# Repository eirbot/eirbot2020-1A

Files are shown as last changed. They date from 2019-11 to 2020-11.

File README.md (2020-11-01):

# EIRBOT 2020-1A : Equipe EIRBOAT 

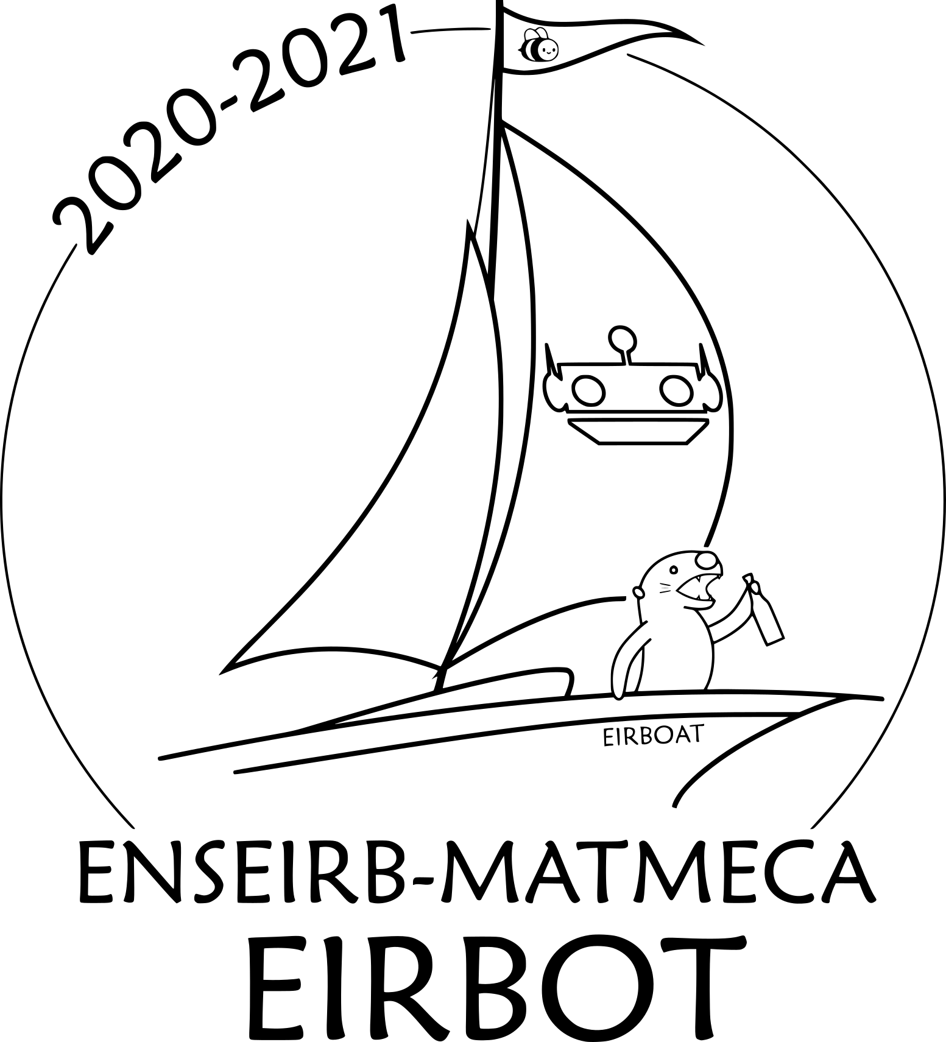
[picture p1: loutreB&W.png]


---

Résultat de l'équipe à l'édition d'octobre 2020 : 24 ième / 51
---

Ceci est le dépôt de l'équipe de 1A de l'association de robotique Eirbot. La
description de l'avancement des différents projets est disponible via la 
[descrition](https://github.com/eirbot/eirbot2020-1A/blob/master/description/descrption.pdf) de nos projets. Le projet se divise en plusieures catégories allant du plus bas au plus au niveau (en terme de raprochement avec le côté physique). 

## Membres
Ce projet est réalisé par les différents membres de Eirbot en première année : 
- Alberty Maxime (SEE)
- Barrais Marius
- Camberlin Erwann (Matmeca)
- Delpeuch Sébastien (Informatique)
- Mangin Lucas
- Moroy Liam
- Neveu Emile
- Pouget Filipe
- Poupon Julien
- Savary Clément (SEE)
- Vaquori Yohann
- Vidal Martin

## Installation 
Le projet est construit avec Cmake, il suffit donc de cloner le projet puis 

```
cd eirbot2020-1A/code/
cd build/
cmake .. 
```

## Éxecution 

Depuis le dossier `build/`

Pour compiler le projet il suffit de faire `make project` en ayant un compilateur
de C++.

Plusieurs méthodes permettent d'exécuter le projet.

En local un `./project` suffit, si la nucléo est branchée via le port USB une
simulation de communication est enclenchée (la nucléo renvoie toujours vrai à
chaque demande). Cela peut demander de faire la commande en super utilisateur ou
changer le chemin d'accès au port USB (ligne 110 de ce
[code](https://github.com/eirbot2020-1A/tree/master/code/rasp/src/main.cc)). 

Pour mettre le projet sur la rasp et donc le robot il faut être connecté au même
wifi que la raspeberry puis faire un `make final`.

En plus de l'exécution des tests sont effectués sur les codes, ils peuvent être
compilés en faisant `make test` puis `./test`. A partir de ce moment des tests
sur tous les modules implémentés sont exécutés, le coverage actuel est de 87%

Finalement un `make doc` permet d'afficher la documentation de nos codes.
Elle est de plus disponible sur notre [page web](https://eirbot.github.io/eirbot2020-1A/md__r_e_a_d_m_e.html)

## Description du projet 
### Mécanique
La mécanique du projet se base sur une architecture octogonale structuré par des
profilés avec la notion d'étage. 

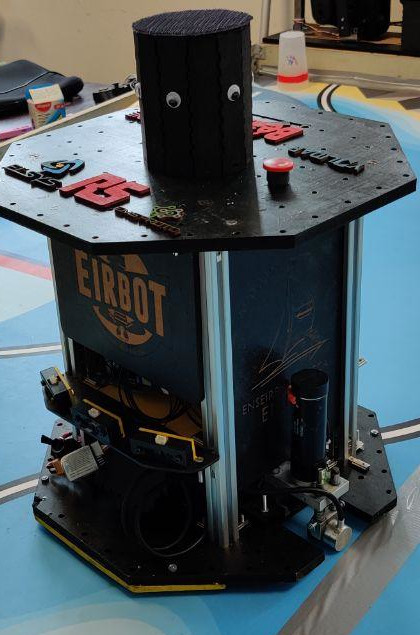
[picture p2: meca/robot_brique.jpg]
robot


### Alimentation 
Un autre étape cruciale de notre robot est la distribution de l'énergie dans ce dernier. Pour ce faire nous passons via une carte d'alimentation, so rôle est de distribuer aux différentes instances l'énergie nécessaire pour fonctionner. 
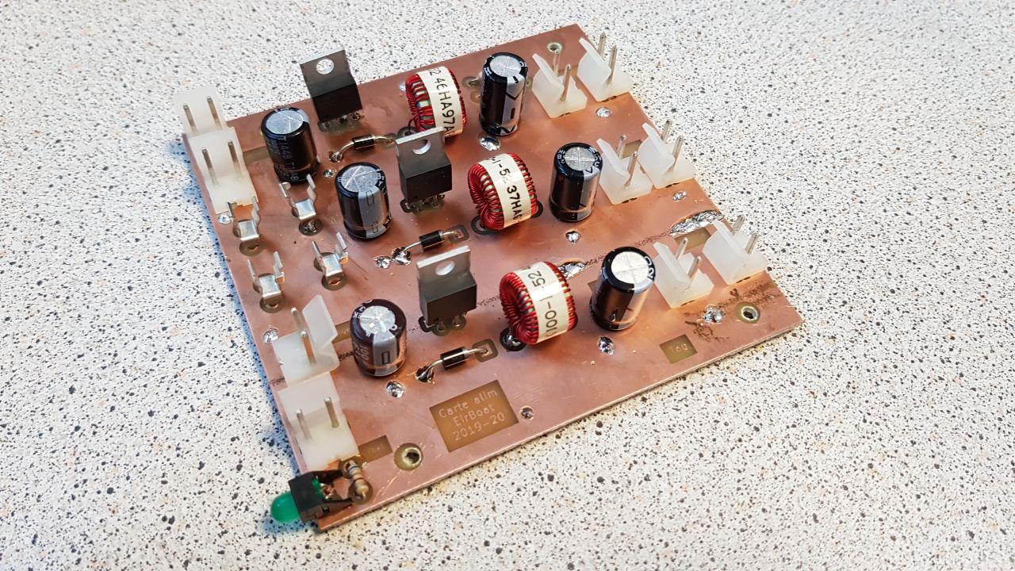
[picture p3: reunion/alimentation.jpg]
résultat alimentation


### Actionneur
Pour réaliser les différentes actions nous avons besoins de différents
actionneurs. 

Tout d'abord des actionneurs simples utiles pour activer le phare et les manches
à air, ils sont au nombre de deux pour gérer facilement chaque côté de la table.

Ensuite un actionneur représentant le pavillon et permettant de lever le
drapeau.

### Puissance 
Une fois que nous pouvons alimenter tous les composants de notre robot nous devons encore permettre un contrôle de la puissance fournie au moteur, pour cela nous créons deux cartes possédant un pont en H, cela nous permet de délivrer la puissance nécessaire à nos moteurs pour nos robots.

### Asservissement
L'idée maintenant que nous avons une mécanique propre, nos différents modules aliméntés et que nous pouvons contrôler précsiement nos moteurs est de créer un asservissement. Le but de l'[asservissement](https://github.com/eirbot/eirbot2020-1A/tree/master/code/nucleo) est de récupérer les informations des encodeurs et de permettre au robot d'atteindre une certainne position tout en gérant l'angle, la puissance des moteurs etc.

### Stratégie
Maintenant que nous avons un asservissement nous devons réaliser les choix pour
notre stratégie. 

La stratégie se décompose en deux parties. Une partie sur la nucléo contenant
les actions "matérielles" à faire (par exemple tourner le servomoteur de
l'actionneur pour la phare). Et une partie de stratégie plus abstraite sur
raspeberry. 

La partie abstraite a plusieurs rôles 
+ Elle contrôle le déroulement de la partie (initialisation, ordre des actions,
  demandes de déplacements ...)
+ Elle gère la communication avec la balise lisant la boussole et le phare 
+ Elle est la seule à connaître la disposition de la table (disposition des
  obstacles, place des ecocups initialement)
+ Elle est capable de calculer une trajectoire entre les obstacles (via un
  algorithme de pathfinding l'A*)
+ Elle est capable de définir dans quel sens il faut ramasser les ecocups
  (probleme du voyageur de commerce, algorithme des colonies de fourmis)
  
Les codes sont disponibles
[ici](https://github.com/eirbot/eirbot2020-1A/tree/master/code/rasp/src). 

### Protocole de communication

Comme dit précédemment nous avons séparé la partie d'implémentation du contrôle
physique (sur la nucléo) et la partie d'implémentation de la stratégie (sur la
rasp). Cela implique donc une communication entre les deux cartes. L'idée est
d'utiliser un protocole de communication du type maitre esclave. Par exemple
lorsque la rasp a trouvé la trajectoire demandé, elle fournit au fur et à mesure
les coordonnées qu'elle souhaite atteindre à la nucléo. Cette dernière via
l'asservissement déplace le robot à la position souhaitée, elle a un certains
temps pour le faire. Si elle arrive à la position demandée elle renvoie "OK", si
elle n'y arrive pas automatiquement le protocole renvoie "TIMEOUT". Si les GP2,
reliés à la nucléo détectent un robot ennemi pendant le déplacement, la nucléo
stoppe le robot et renvoie "DETECTION" à la rasp. Cette dernière prendra alors
les mesures nécessaires pour éviter le robot. C'est ainsi que se déroule la
communication entre la rasp et la nucleo. 

## Phare
En marge du robot nous devons réaliser l'expérience. L'objectif du phare est de se déployer pendant le match pour permettre d'atteindre une certainne hauteur. Cela est réalisé par un bras robotique imprimé en PLA. Ce dernier possède un design comme suit.
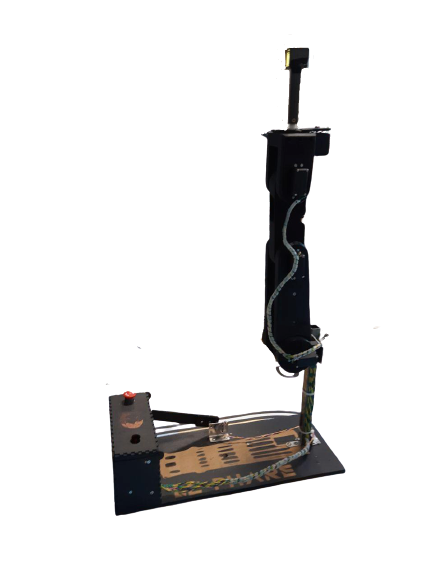
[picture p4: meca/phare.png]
phare


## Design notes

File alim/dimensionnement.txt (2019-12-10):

datasheet buck :
http://www.ti.com/lit/ds/symlink/lm2576hv.pdf

Moteurs : 3A/moteurs -> largeurs des pistes
Logique 5V 1.5A : 150uH
Puissance 5V 3A: 100uH 
Puissance 12V 3A : 100uH (ajouter en série feedback 5.74kOhms

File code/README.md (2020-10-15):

# Cross compilation

* `cmake ./ -DCMAKE_TOOLCHAIN_FILE=toolchain.cmake`
* `make upload` upload et execute test  sur rasp
* `make final` upload et execute project sur rasp
* Se connecter au téléphone : EirboatAP , mdp : nmreglhvbc

# Eviter de se taper le mot de passe ssh à chaque fois

* générer la clé : `ssh-keygen`
* copier la clé sur la rasp: `ssh-copy-id pi@eirboat`

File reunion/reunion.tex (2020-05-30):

\documentclass[a4paper,10pt]{report}
\usepackage[utf8]{inputenc}
\usepackage[T1]{fontenc}
\usepackage[french]{babel}
\usepackage{graphicx}
\usepackage{ulem}
\usepackage{float}
\usepackage{amsmath}
\usepackage{amssymb}
\usepackage{mathrsfs}
\usepackage{color}
\usepackage{fancyhdr}
\usepackage{pdfpages}
\usepackage{layout}
\usepackage{multicol}
\usepackage{setspace}
\usepackage{tabularx,array}
\usepackage{tikz, tkz-tab}
\usepackage[top=2cm,bottom=2cm,left=2cm,right=2cm]{geometry}
\usepackage[colorlinks=true]{hyperref}
\usepackage{amsthm}
\usepackage{listings}
\setlength{\parindent}{0cm}
\setlength{\parskip}{1ex plus 0.5ex minus 0.2ex}
\newcommand{\hsp}{\hspace{20pt}}
\newcommand{\HRule}{\rule{\linewidth}{0.1mm}}
\usepackage{transparent}
\usepackage{eso-pic,graphicx}

\AddToShipoutPicture{%
  \unitlength=1cm
    \put(1.6,8){\transparent{0.3}\includegraphics[width=18cm,
        height=13cm]{filigramme.png}}
  }

\newcolumntype{Y}{>{\centering\arraybackslash}X}
\begin{document}
\begin{spacing}{1.5}
\graphicspath{{image/}}
\begin{titlepage}
\begin{sffamily}
\begin{center}
\vspace*{\stretch{1}}
\textsc{\LARGE Eirbot \\ Coupe de France de robotique}\\[2cm]
\HRule \\[0.4cm]
{\huge \bfseries Equipe Eirboat \\[0.4cm]}

\HRule \\[2cm]

\textsc{\Large 1A 2019-2020}\\[2cm]
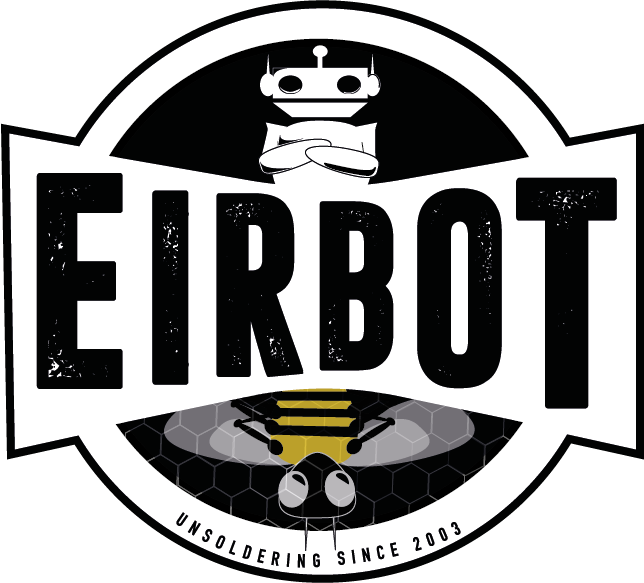
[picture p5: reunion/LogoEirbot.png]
               \vfill

\vspace*{\stretch{1}}
  \end{center}
  \end{sffamily}
\end{titlepage}

\setcounter{tocdepth}{1}
\newpage
\part{Rapports de réunion}
\pagestyle{fancy}
\lhead{Eirboat}
\chead{\textbf{Rapports de réunion}}
\rhead{\thepage}
\lfoot{}
\cfoot{}
\rfoot{}

\section*{Jeudi 24 Octobre}
\paragraph*{Ordre du jour.}
\begin{itemize}
\item Définir les différentes tâches que doit remplir le robot
\item Donner une première idée de ce que les gens doivent faire
\end{itemize}
\begin{multicols}{2}
\paragraph*{Tâches à faire par le robot.}
Une version détaillée est disponible en \ref{taches}
\begin{itemize}
\item Se mouvoir (soft)
\item Mécanique générale
\item Détecter les adversaires
\item Détecter les objets
\item Lire la boussole
\item Communiquer
\item Elever le drapeau
\item Actionner les manches à air
\item Alimentation
\item Phare
\end{itemize}
\columnbreak
\paragraph*{Répartition des tâches.}
Une version détaillé est disponible en \ref{repartition}
\begin{itemize}
\item Liam, Emile, Clément, SD
\item Erwann, Valentin, Marion
\item Martin, Liam
\item $\emptyset$
\item Maxime, Emile, Léo
\item SD
\item Filipe, Valentin, Erwann
\item Filipe, Jeremy, Marius
\item Ptit Lu, Yohann, Julien, Léo
\item Marius, Marion
\end{itemize}
\end{multicols}

\paragraph*{Objectifs de la prochaine réunion.}
\begin{itemize}
\item Spécifier les robots
\item Définir précisément les tâches
\item Penser à la stratégie
\end{itemize}

\newpage
\section*{Jeudi 31 Octobre}
Pas de réunion : vacances
\newpage
\section*{Jeudi 7 Octobre}
\paragraph*{Ordre du jour.}
\begin{itemize}
\item Définir les actions à faire
\item Définir une hiérarchie de difficulté dans les actions
\item Définir la mécanique du robot
\end{itemize}

\paragraph*{Définition des méthodes.}
\begin{center}
\begin{tikzpicture}
\tikzstyle{lien}=[->,>=stealth,rounded corners=20pt,thick]
\tikzset{individu/.style={draw,thick,fill=#1!25},
individu/.default={white}}
\node[individu=red] (A) at (0,0 ){\textsc{Détecter adversaire}};
\node[individu] (A1) at (4,1){Système infrarouge};
\node[individu] (A2) at (4,-1 ){\xout{Système LIDAR}};
\draw[lien] (A) -- (A1);
\draw[lien] (A) -- (A2);

\node[individu=red] (B) at (10,0 ){\textsc{Lire Boussole}};
\node[individu] (B1) at (14,1){Balise sur le côté};
\node[individu] (B2) at (14,-1 ){Détecteur sur le robot};
\draw[lien] (B) -- (B1);
\draw[lien] (B) -- (B2);

\node[individu=green] (C) at (0,-5 ){\textsc{Elevation drapeau}};
\node[individu] (C1) at (5,-5){Pignon, cremaillère, ressort};
\draw[lien] (C) -- (C1);

\node[individu=green] (D) at (10,-5 ){\textsc{Manche à air}};
\node[individu] (D1) at (14,-5){Tige qui sort du robot};
\draw[lien]  (D) -- (D1);

\node[individu=orange] (E) at (5,-7 ){\textsc{Phare}};
\node[individu] (E1) at (9,-7){Voir avec Marius};
\draw[lien]  (E) -- (E1);

\node[individu=orange] (F) at (5,-9 ){\textsc{Mécanique générale}};
\node[individu] (F1) at (1,-11){Forme : octognone};
\node[individu] (F2) at (5,-11){Taille : en cours};
\node[individu] (F3) at (9,-11){Motricité : 2 roues + patins};
\draw[lien]  (F) -- (F1);
\draw[lien]  (F) -- (F2);
\draw[lien]  (F) -- (F3);
\end{tikzpicture}
\end{center}

\paragraph*{Description du robot.}
Pour l'instant il se dessine selon 5 étages
\begin{enumerate}
	\item Switch pour le côté de jeu, diode de vérification, porte balise, ON/OFF, Boutons d'arrêt d'urgence.
	\item Porte pavillon, rasp
	\item Porte pavillon, carte numérique
	\item Détecteur IR, carte puissance, actionner manche à air, détecteur IR
	\item moteur, batterie, moteur
\end{enumerate}

\paragraph*{Objectif de la prochaine réunion.}
\begin{itemize}
	\item Avancement table
	\item Avancement méca
	\item Lancer le phare
	\item Lancer l'asservissement
\end{itemize}

\newpage
\section*{Jeudi 14 Novembre}
\paragraph*{Point mécanique.}
Erwann à produit un prototype du robot, il n'est pas complet mais nous donne une idée de ce que nous allons faire. La création du robot est donc en cours.
Pour les premiers test, nous pouvons utiliser la base métallique.

\paragraph*{Point phare.}
La mécanique du phare est au point, il faut rajouter un module de musique, l'actionneur sera identique à celui des manches à air.
Sur le planning le phare pourrait être construit d'ici la prochaine réunion.

\paragraph*{Point asservissement.}
Liam, Emile et Clément commencent à travailler dessus. Ils se sont familiarisés avec les encodeurs et chapterent sur la nucléo.\\
Un résumé de la formation de Mathieu sur l'odométrie : \\
On définit $v_L$ , $v_R$ comme la vitesse gauche et la vitesse droite.
\begin{itemize}
  \item $\text{short} \; v = (\text{short} \; v_{old} - \text{short} \; v_{new})$ %v doit posséder un type de la même dimension que old et new, old et new doivent être du même type
  \item Soit $d$ la distance infinitésimal $$d = \dfrac{v_L+v_R}{2}$$ Soit $\alpha$ l'angle infinitésimal $$\alpha = \dfrac{v_L-v_R}{2}$$
  \item Rafraichissement de la position du robot. \\ Soit $x,y,\theta$ les coordonnées du robot. \begin{enumerate}
  \item $\theta = \theta + \dfrac{\alpha}{2}$
  \item $\begin{cases} x = x + cos(\dfrac{\alpha}{\text{TICKS}}) \times d \\ y = y + sin(\dfrac{\alpha}{\text{TICKS}}) \times d \end{cases}$
  \item $\theta = \theta + \dfrac{\alpha}{2}$
  \item $\text{if}(\text{aps}(\theta) > \pi.\text{TICKS PER RAD})$ \\ $a=a-\text{sg}(a)\times 2 \pi \times \text{TICKS}$
  \end{enumerate}
\end{itemize}
Toutes les codes et les explications sont disponibles sur le github : \url{https://github.com/eirbot/eirbot2019-2A/tree/master/soft/include}

\newpage
\section*{Jeudi 21 Novembre}
Open perdu

\newpage
\section*{Jeudi 28 Novembre}
\paragraph*{Point Mécanique.}
La table est bien avancée, il ne reste plus qu'à fixer les derniers éléments (le
meuble pour les gobelets c'est le feu). Emile n'a plus le droit de toucher au
bois et à la découpe laser en même temps suite à ses exploits pour tenter de
graver ma tête. \\
Niveau robot, le design du robot est acté, on chapter sur une base et un toit
octogonal, les étages seront carré. On attend Nans pour la commande des
profilés. La base avec les moteurs peut chapterir en production.

\paragraph*{Point phare.}
\label{sec:phare}
Nous avons un doute sur l'homologation du premier phare, il sera donc transformé
en canon quand on aura changé le moteur. \\
Concernant le nouveau phare l'idée était de chapterir sur un bras robot (Nans sera
content).

\paragraph*{Point Asservissement + Info.}
Le choix de l'odométrie à été posé, la table sera modélisée comme une grille. Le
robot pourra se déplacer à chaque intersection de la grille sera un point où le
robot pourra se déplacer.\\
\begin{center}
  \begin{tikzpicture}
    \tikzstyle{lien}=[->,>=stealth,rounded corners=20pt,thick]
  \draw[very thin, gray] (0,0) grid[step=0.5] (7.5,5);
  \draw[very thin, blue] (0,0.5) node [left]{Port allié} grid[step=0.5] (1,3.5) ;
  \draw[very thin, red]  (6.5,0.5) grid[step=0.5] (7.5,3.5) node [right]{Port adverse};
  \draw [rotate=2,green!50!black] (1.5,4) --
  (2,4.5)--(2.5,4.5)--(3,4)--(3,3.5)--(2.5,3)--(2,3)--(1.5,3.5)--cycle;
  \draw [lien,orange,rotate=2] (2.75,3.25) -> (4.5,2);
\end{tikzpicture}
\end{center}
Niveau software l'idée est de commencer par créer un serveur ssh entre une rasp
et un ordinateur. Combiné à un protocole de communication entre une rasp et une
nucléo on peut espérer pouvoir coder le robot à distance. L'interface de
contrôle du robot commence à être pensée. \\
Suite à une discution avec Matthieu, un algorithme de path fouding commence à se
dessiner sur un base Astar.\\ Pour l'instant l'informatique à juste fait un
phare en Ascii.
\newpage
\begin{figure}[!h]
  \center
  \begin{lstlisting}
     .n.
    /___\
    |  o|
   IIIIIII
    |  /|
    | / |
    |/  |
    |  /|
    | / |
    |/  |
  \end{lstlisting}
\end{figure}
\paragraph*{Point Alimentation.}
La carte d'Alimentation a été pensée, le groupe s'occupant de cette dernière
recherche un moyen de travailler sur Kicad en groupe. \textit{Elle est où la
  carte ?}.
\begin{figure}[h!]
  \center
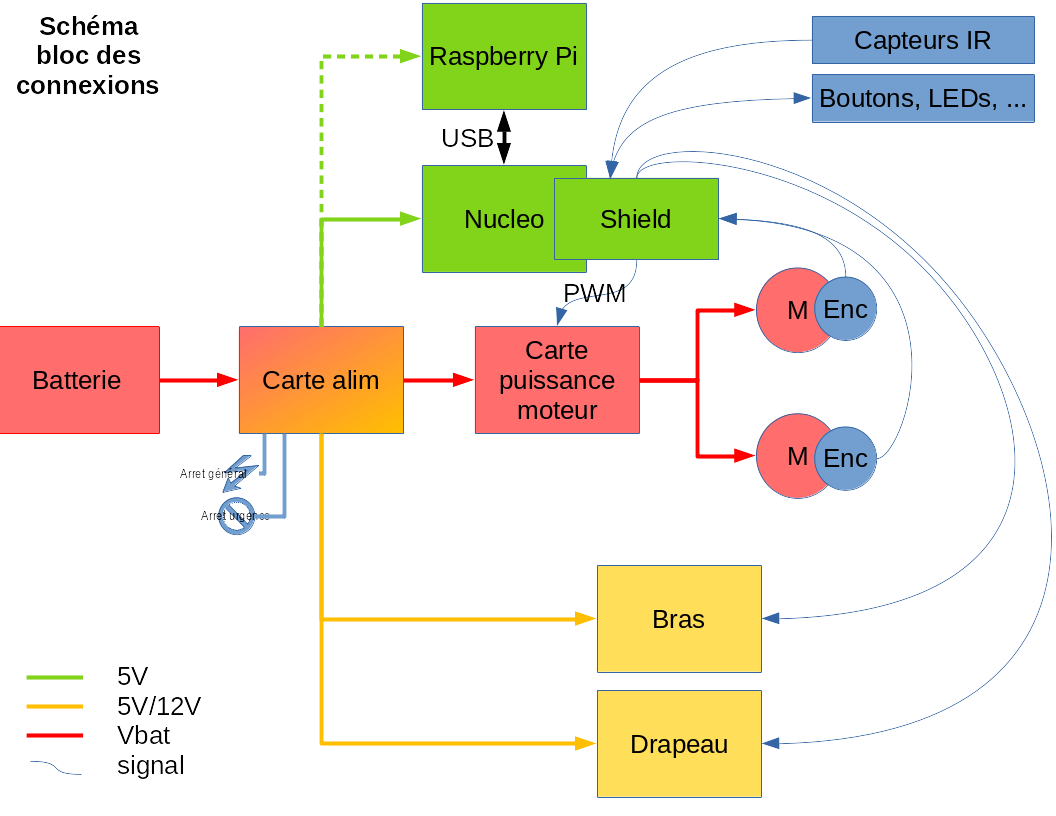
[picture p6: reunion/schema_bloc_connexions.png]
  
  \caption{Schéma de principe de l'alimentation}
\end{figure}

\paragraph*{Point Puissance.}
Nous réutilisons les moteurs des 2A, le groupe travaillant dessus commence à
travailler.

\paragraph*{Point actionneur.}
Cnf tenaq pubfr à qver

\newpage
\section*{Jeudi 5 Décembre}
C'est bientôt Noël
\paragraph*{Point Table.}
Tous les éléments sont découpés et assemblés. Les manches à air sont montés et
la boussole est en cours de montage. Il restera les balises et au un écueil.

\paragraph*{Point Mécanique.}
L'étage du bas est modélisé, en attente de découpage. Nans a commandé les
profilés, la base pourra donc être montée sous peu.

\paragraph*{Point Phare.}
Le projet de l'ancien phare est correctement entéré. Marius est parti sur un
nouveau phare avec une base de bras robot comme ci contre.
\begin{figure}[H]
  \center
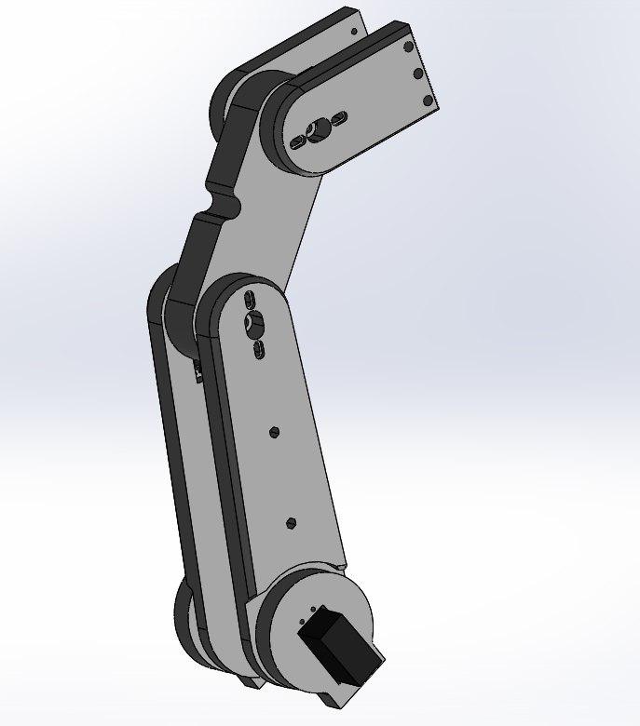
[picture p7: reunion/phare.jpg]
  
  \caption{Version 2 du phare}
\end{figure}

\paragraph*{Point Asservissement + Info.}
Sébastien et Emile se battent avec le C++, Emile travaille sur les informations
renvoyées par les encodeurs pendant que Sébastien réflechit aux structures
qui permettrons au robot de correctement se déplacer.

\paragraph*{Point Alimentation.}
La carte d'alimentation avance bien, le travail de conception est en cours le
schéma de la carte d'alimentation sera disponible la semaine prochaine.

\paragraph*{Point Puissance.}
Y'vqér rfg q'nggraqer Znegva , cnepr dh'vy nvzr znatre qrf enqvngrhef nanybtvdhrf

\paragraph*{Point Actionneur.}
Les actionneurs sont au point morts pour l'instant, ce n'est pas l'urgence.

\newpage
\section*{Jeudi 12 Décembre}
Y avait du monde
\paragraph{Point Mécanique.}
Le dossier github de le méca a été crée et actualisé, on attend les profilés.
\paragraph{Point Phare.}
Le phare est en cours d'impression cela va prendre plusieurs jours.
\paragraph{Point Puissance.}
Le code de contrôle des moteurs a été conçu par Emile. L'utilisation de deux
ponts en H (LMD18200) est actée. Les moteurs fonctionnent en 16V ils seront donc
directement mis sur la batterie. La communication entre Ptit Lu et Martin est
faite.
\paragraph{Point Asservissement.}
L'idée est plutot d'attendre Clément et son expérience. Emile a testé les deux
moteurs ils sont bons, les encodeurs sont en cours de test. Grâce à Matthieu,
Emile arrive à utiliser la Nucléo. Le code a été commencé, Liam réfléchit à la
théorie de manière assez poussée.
\paragraph{Point Informatique.}
Grâce à OpenClassRoom Sébastien sait faire du C++ (enfin en théorie).
L'algorithme de recherche de chemin est semi-implémenté grâce au projet ours.
L'interface du robot n'a pas commencé.
\paragraph{Point Alimentation.}
Ptit Lu a dit : ``Mangez 5 fruits et légumes, c'est bon pour la santé.''
Le rootage de la carte doit débuter ce soir et on met pas de radiateur pour
faire en sorte que le robot ait plus de chance de bruler. Le récapitulatif du
schéma électrique est disponible dans les descriptions.

\newpage
\section*{Jeudi 16 Janvier}
\paragraph{Point Mécanique.}
La base du robot a été découpé ce jeudi. Le montage devrait avoir lieu dans la semaine
\paragraph{Point Phare.}
Le phare est en cours d'impression cela va prendre plusieurs jours. Mais il est
stylé de ouf.
\paragraph{Point Puissance.}
Le design est fait à priori.
\paragraph{Point Asservissement.}
Retour de Clément ! Il a fabriqué un banc de test et commencer à tester quelques
codes. Alban a dispensé une petite formation sur mbed pour les aider.
\paragraph{Point Informatique.}
Discussions sur le protocole de communication entre la Raspberry Pi et la
Nucléo. Utilisation d'une liaison série (via USB sûrement).
Présentation des avancements de la stratégie et schéma récapitulatif de cette dernière :
\begin{center}
  \begin{tikzpicture}
  \tikzstyle{lien}=[->,>=stealth,rounded corners=20pt,thick]
\tikzset{individu/.style={draw,thick,fill=#1!25},
individu/.default={white}, rounded corners=4pt}
\node[individu=violet] (A) at (0,0){\textsc{Main}};
\draw(1,0) node[right]{Envoie les ordres};
\draw(1,-0.5) node[right]{au fur et à mesure};
\node[individu=blue!50!black] (B) at (0,2){Navigation};
\draw(1,2) node[right]{$\leftarrow$ Calcul d'un};
\draw(1,1.5) node[right]{\; \; chemin précis};
\draw(-1,2) node[left]{Transformation en $\leftarrow$};
\draw(-1,1.5) node[left]{chemin global \;\;\;};

\node[individu=blue] (C) at (3,4){World};
\draw (4,4) node[right]{Renseigne position};
\draw (4,3.5) node[right]{obstacles};
\node[individu=green] (D) at (-3,4){Asservissement};
\draw (-4.5,4) node[left]{Permet d'envoyer};
\draw (-4.5,3.5) node[left]{requete déplacement};
\node[individu=blue!50!black] (E) at (-4,0){Evitemment};
\draw (-5,0) node[left]{Court circuite};
\draw (-5,-0.5) node[left]{le main};
\node[individu=green] (F) at (-3,-2){Détection};
\draw (-3,-2.5) node[below]{Renseigne GP2};
\node[individu=green] (G) at (3,-2){Actionneur};
\node[individu] (H) at (3,-4){Affichage};

\draw[lien] (A) -- (B);
\draw[lien] (A) -- (F);
\draw[lien] (A) -- (G);
\draw[lien] (F) -- (A);
\draw[lien] (B) -- (D);
\draw[lien] (C) -- (B);
\draw[lien] (E) -- (B);
\draw[lien] (F) -- (E);

  \end{tikzpicture}
\end{center}

\paragraph{Point Alimentation.}
La 3ème tentative de fabrication de la carte d'alimentation a réussie (L'auteur
de ce rapport en a quand même raté deux :)) ! Perçage fini et soudures finies jeudi soir.

\newpage
\section*{Jeudi 23 Janvier}
(C'est mon anniversaire quand je tape se rapport, vous vous en foutez mais bon
:'), en plus vous comprennez pas qui est l'auteur, une fois Ptit Lu, une fois
moi, on est perdu)
\paragraph{Point Mécanique.} La découpe laser est cassée, Erwann devrait continuer la modélisation des étages
\paragraph{Point Alimentation.} La carte est finie, il faut tester la carte et
surtout penser aux cables , la gestion des cables devrait être gérée par Julien.
\paragraph{Point Puissance.} Martin n'a plus qu'à les imprimer (peut être aidé
par Julien) il faut vérifier l'empreinte des composants.
\paragraph{Point asservissement.} Liam a commencé le codage et la création des
classes, on a plutot tapé sur le haut niveau, il manque le traitement des
données par Clément. Emile a crée une conversation messenger (preuve de son
utilité moindre)
\paragraph{Point protocole de com.} (pourquoi c'est pas toi qui tape ce rapport
?) Le protocole est TRES bien avancé, on peut envoyer et recevoir des données
mais ça beug un peu
\paragraph{Point actionneur.} Filipe a travaillé !! (il a fait un pignon on se
chauffe pas trop non plus)
\paragraph{Point phare.} (Il est beau !!) On a imprimé 6 pièces sur 7 , il faut
encore créer la carte d'alimentation
\paragraph{Point information.} Il y a eu un peu de changement dans le principe,
maintenant lors d'une requete de déplacement l'asserv peut renvoyer : ``ok'',
``timeout'' ou ``detection'' cela a permis de fusionner facilement la détection
et la navigation.
\paragraph{Point compteur.} On a compris qu'il fallait compter les points,
julien s'en occupe.

\newpage
\section*{Jeudi 6 Février}
C'est le première réunion en salle de réunion, c'était sympa
\paragraph{Point Mécanique.}
A cause de la panne de la découpe laser les profilés n'ont pas pu être installé.
On félicite Erwann pour le défaut de conception sur les manches à Air :).
Plusieurs objectifs ont été fixé. Tout d'abbord Erwann devrait concevoir les
supports de GP2. Il commence aussi à réflechir à la méthode de construction de
la balise.
\paragraph{Point Alimentation.} Le cas général fonctionne très bien. Il faut
encore tester les cas critiques et commencer à les installer sur le robot.
\paragraph{Point Puissance.} Martin et Filipe travaillent désormais ensemble.
Ils se sont fixés deux semaines pour sortir une première version des cartes.
\paragraph{Point Shield.} (Oui c'est un nouveau point) Yohann à réalisé une
bonne partie de la conception, maintenant il faut qu'il récupère les
informations de tout le monde pour être sur de réaliser un shield précis. La
quête des informations commence.
\paragraph{Point Asservissement.} Il a passé 3 heures à installer MatLab,
malgrès sa modestie l'asservissement avance très bien. Le robot arrive à être
commandé (sans faire n'importe quoi), Matthieu l'a aidé pour faire une méthode
de caractérisation des moteurs. Cela prend du temps mais il avance très bien.
\paragraph{Point Stratégie.} Nous avons fait le lien entre la stratégie et le
protocole de Communication, actuellement lorsque la stratégie envoie une requête
à la nucléo, la requête est très bien envoyée et le retour est pour l'instant générique.
\paragraph{Point Nucléo.} Il faut réalisrr le cahier des charges pour Liam, il devra
gérer les GP2 (activation / desactivation, gérer la récupération des informations
), gérer les contacteurs et les actionneurs.
\paragraph{Point Phare.} IL EST BEAU !!! Il manque une pièce (le haut du phare),
il reste à faire le circuit imprimé et la communication avec le robot (433MHz).
\paragraph{Point Compteur.} Julien connait la datasheet par coeur, et le schéma
a été commencé sur Kicad.
\paragraph{Global.} L'organisation physique du robot a été pensé.

\newpage
\section*{Jeudi 13 Février}
\paragraph{Point Mécanique.} La découpe laser est réparée !! Le porte batterie
est modélisé et en cours d'impression. Les profilés vont pouvoir être installé
sous peu et les supports GP2 ne sont pas commencés. \\

\paragraph{Point Alimentation.} ``NON''.

\paragraph{Point Puissance.} Conception commencée.

\paragraph{Point Shield.} Il a commencé la conception mais il attend que l'on soit sur
de tous les pins etc.

\paragraph{Point Asservissement.} Clément a pratiqué Matlab et il a trouvé les
équations il faut encore faire les réglages du correcteur

\paragraph{Point Stratégie.} Il faut encore changer quelques trucs (comme la
prise en compte de la distance pour les obstacles)

\paragraph{Point Nucléo.} La réunion avec Liam a été effectuée, le travail reste
à faire

\paragraph{Point Phare.} Une solution pour l'éclairage a été trouvé, avec une
led 1W et un système de miroir comme un phare réel.

\newpage
\section*{Jeudi 20 Février}
Pas de réunion : finir dossier Cdiscount

\newpage
\section*{Jeudi 27 Février}
\paragraph{Point Mécanique.} Clément : \og la méca c'est de la merde\fg{} il y a
un problème dans l'engrenage, dans les moteurs, faire en sorte de ne pas avoir
une vibration trop grande, il faut refaire le premier étage.
\paragraph{Point Asservissement.}  L'asservissement en vitesse de chaque moteur
est plutôt bonne. Il faut maintenant penser à un asservissement central par
rapport aux deux moteurs et non par rapport à chaque moteur.
\paragraph{Point Alimentation.} Il faut rajouter un fusible et voir la longueur
des cables.
\paragraph{Point Phare.} Marius attend l'arrivée des leds (il est beau le phare)
\paragraph{Point Communication.} On verra plus tard, \og ta gueule sèb\fg{}

\newpage
\section*{Jeudi 5 Mars}
Vacances, je peux faire une réunion tout seul mais bon

\newpage
\section*{Jeudi 12 Mars}
\paragraph{Point Mécanique.}
\begin{itemize}
  \item bloc moteur : avec nans pendant les vacances, ils ont fait un piece et
  elle est mieux que Hugo.
  \item Est ce qu'on refait la base ? Le modele d3D est fait , Si clément se
  chauffe pour refaire les trucs ça peut être pas mal. Pas commencé support GP2,
  mais d'abord les étages
\end{itemize}
\paragraph{Point Alimentation.}
Les fusibles ont été rajoutés mais Nans est un tocard. C'est quand qu'on la
monte ? Je comprend pas tout quand les élecs parlent.
\paragraph{Point Puissance.}
On a fait cramer un pont en H (c'est 7 euros),si y a pas la coupe on peut
transformer le truc en table apéro.
\paragraph{Point Phare.}
On attend les LEDS
\paragraph{Point Asservissement.}
Il va bientot passer à l'asserv de position.
\paragraph{Point Nucléo.}
On s'amuse avec le bas niveau
\paragraph{Point détection.}
Commencer à étaloner le signal de sorti du GP2 parce qu'il fait de la merde.
\paragraph{Point Protocole.}
Il commence à faire le lien avec les différents trucs.
\paragraph{Point Raspberry.}
ca marche c bon
\paragraph{Point Actionneurs.}
On va mettre 2 actionneurs en fait parce que c'est bien et seb galère avec des
servo de merde
\paragraph{Point compteur.}
J'ai rien branlé du compteur
\paragraph{Question 3A.} ra snvg ba prafher çn \og wr fnvf cnf ?\fg{}
\paragraph{En fait Nans parle.} Du coup faut attendre 20h, mais en gros tous le
monde commence à penser que y a moyen que y ait pas de coupe, même on organise
un mini eirbot chez Sèb, il a l'air chaud.
\newpage
\end{spacing}
\end{document}

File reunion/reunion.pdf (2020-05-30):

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

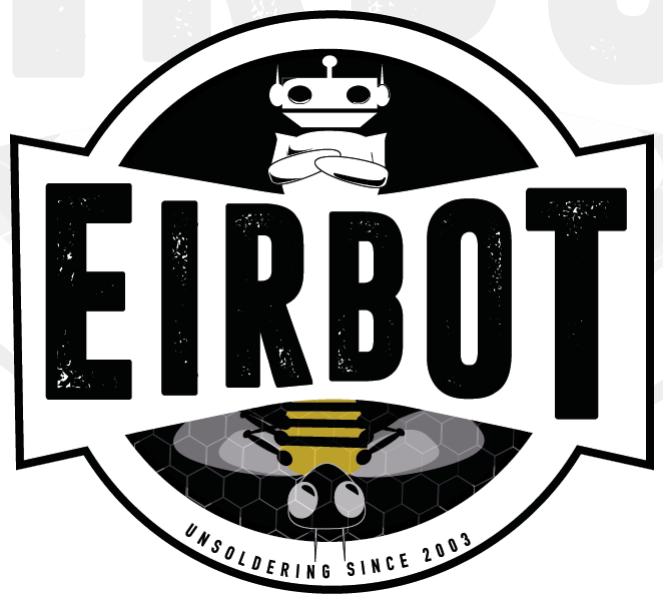
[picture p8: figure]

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

Eirboat | Rapports de réunion | 2

Jeudi 24 Octobre

Ordre du jour.

Dénir les diérentes tâches que doit remplir le robot

Donner une première idée de ce que les gens doivent faire

Tâches à faire par le robot. Une version détaillée

est disponible en ??

Se mouvoir (soft)

Mécanique générale

Détecter les adversaires

Détecter les objets

Lire la boussole

Communiquer

Elever le drapeau

Actionner les manches à air

Alimentation

Phare

Répartition des tâches. Une version détaillé est

disponible en ??

Liam, Emile, Clément, SD

Erwann, Valentin, Marion

Martin, Liam

∅

Maxime, Emile, Léo

SD

Filipe, Valentin, Erwann

Filipe, Jeremy, Marius

Ptit Lu, Yohann, Julien, Léo

Marius, Marion

Objectifs de la prochaine réunion.

Spécier les robots

Dénir précisément les tâches

Penser à la stratégie

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

Jeudi 7 Octobre

Ordre du jour.

Dénir les actions à faire

Dénir une hiérarchie de diculté dans les actions

Dénir la mécanique du robot

Dénition des méthodes.

Détecter adversaire

Système infrarouge

//////////Système//////////LIDAR

Lire Boussole

Balise sur le côté

Détecteur sur le robot

Elevation drapeau | Pignon, cremaillère, ressort | Manche à air | Tige qui sort du robot
Phare | Voir avec Marius

Mécanique générale

Forme : octognone | Taille : en cours | Motricité : 2 roues + patins

Description du robot. Pour l'instant il se dessine selon 5 étages

1. Switch pour le côté de jeu, diode de vérication, porte balise, ON/OFF, Boutons d'arrêt d'urgence.
2. Porte pavillon, rasp
3. Porte pavillon, carte numérique
4. Détecteur IR, carte puissance, actionner manche à air, détecteur IR
5. moteur, batterie, moteur

Objectif de la prochaine réunion.

Avancement table

Avancement méca

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

Jeudi 14 Novembre

Point mécanique. Erwann à produit un prototype du robot, il n'est pas complet mais nous donne une idée

de ce que nous allons faire. La création du robot est donc en cours. Pour les premiers test, nous pouvons utiliser

la base métallique.

Point phare. La mécanique du phare est au point, il faut rajouter un module de musique, l'actionneur sera

identique à celui des manches à air. Sur le planning le phare pourrait être construit d'ici la prochaine réunion.

Point asservissement. Liam, Emile et Clément commencent à travailler dessus. Ils se sont familiarisés avec

les encodeurs et chapterent sur la nucléo.

Un résumé de la formation de Mathieu sur l'odométrie :

On dénit vL , vR comme la vitesse gauche et la vitesse droite.

short v = (short vold − short vnew)

Soit d la distance innitésimal

d =

vL + vR
2

Soit α l'angle innitésimal

α =

vL − vR
2

Rafraichissement de la position du robot.

Soit x, y, θ les coordonnées du robot.

1. θ = θ +

α
2

2.

x = x + cos(

α
TICKS) × d

y = y + sin(

α
TICKS) × d
3. θ = θ +

α
2
4. if(aps(θ) > π.TICKS PER RAD)

a = a − sg(a) × 2π × TICKS

Toutes les codes et les explications sont disponibles sur le github : https://github.com/eirbot/eirbot2019-2A/

tree/master/soft/include (https://github.com/eirbot/eirbot2019-2A/tree/master/soft/include)

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

Jeudi 28 Novembre

Point Mécanique. La table est bien avancée, il ne reste plus qu'à xer les derniers éléments (le meuble pour

les gobelets c'est le feu). Emile n'a plus le droit de toucher au bois et à la découpe laser en même temps suite

à ses exploits pour tenter de graver ma tête.

Niveau robot, le design du robot est acté, on chapter sur une base et un toit octogonal, les étages seront carré.

On attend Nans pour la commande des prolés. La base avec les moteurs peut chapterir en production.

Point phare. Nous avons un doute sur l'homologation du premier phare, il sera donc transformé en canon

quand on aura changé le moteur.

Concernant le nouveau phare l'idée était de chapterir sur un bras robot (Nans sera content).

Point Asservissement + Info. Le choix de l'odométrie à été posé, la table sera modélisée comme une grille.

Le robot pourra se déplacer à chaque intersection de la grille sera un point où le robot pourra se déplacer.

Port allié

Port adverse

Niveau software l'idée est de commencer par créer un serveur ssh entre une rasp et un ordinateur. Combiné à

un protocole de communication entre une rasp et une nucléo on peut espérer pouvoir coder le robot à distance.

L'interface de contrôle du robot commence à être pensée.

Suite à une discution avec Matthieu, un algorithme de path fouding commence à se dessiner sur un base Astar.

Pour l'instant l'informatique à juste fait un phare en Ascii.

. n .
/___\
| o |
I I I I I I I
| / |
| / |
| / | |
| | / |
| / |
| / |

Point Alimentation. La carte d'Alimentation a été pensée, le groupe s'occupant de cette dernière recherche

un moyen de travailler sur Kicad en groupe. Elle est où la carte ?.

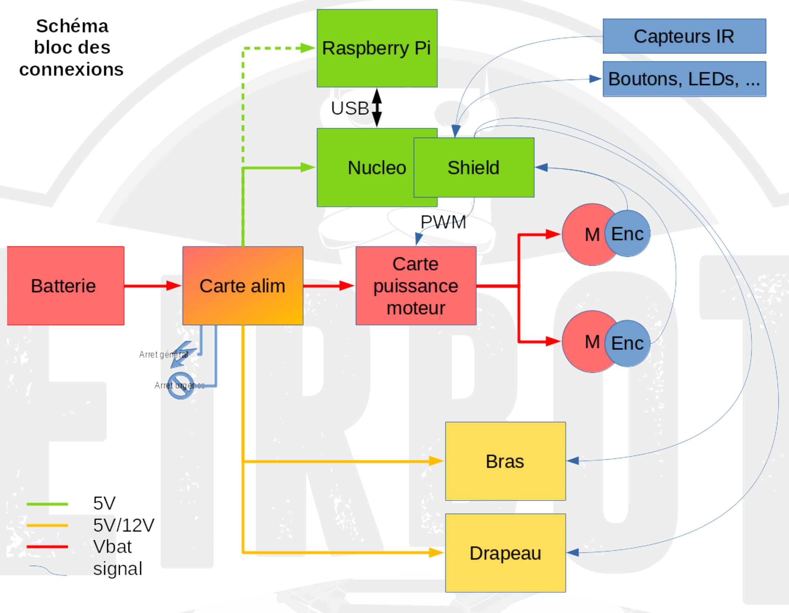
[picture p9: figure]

Figure 1 Schéma de principe de l'alimentation

Point Puissance. Nous réutilisons les moteurs des 2A, le groupe travaillant dessus commence à travailler.

Point actionneur. Cnf tenaq pubfr à qver

Jeudi 5 Décembre

C'est bientôt Noël

Point Table. Tous les éléments sont découpés et assemblés. Les manches à air sont montés et la boussole est

en cours de montage. Il restera les balises et au un écueil.

Point Mécanique. L'étage du bas est modélisé, en attente de découpage. Nans a commandé les prolés, la

base pourra donc être montée sous peu.

Point Phare. Le projet de l'ancien phare est correctement entéré. Marius est parti sur un nouveau phare

avec une base de bras robot comme ci contre.

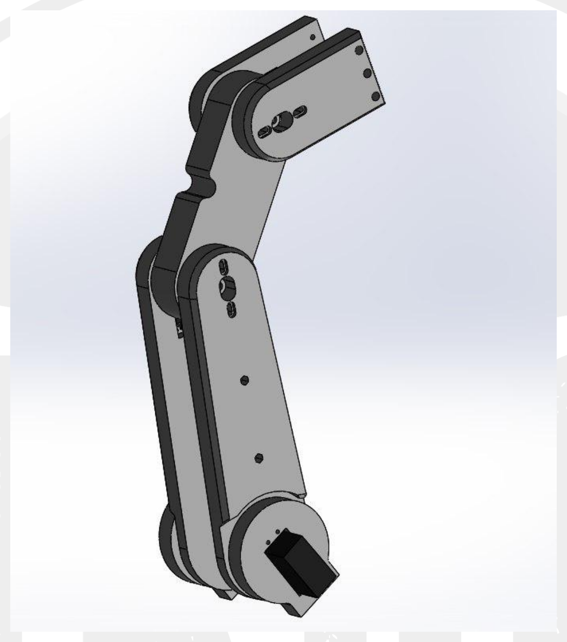
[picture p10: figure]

Figure 2 Version 2 du phare

Point Asservissement + Info. Sébastien et Emile se battent avec le C++, Emile travaille sur les informa-

tions renvoyées par les encodeurs pendant que Sébastien réechit aux structures qui permettrons au robot de

correctement se déplacer.

Point Alimentation. La carte d'alimentation avance bien, le travail de conception est en cours le schéma de

la carte d'alimentation sera disponible la semaine prochaine.

Point Puissance. Y'vqér rfg q'nggraqer Znegva , cnepr dh'vy nvzr znatre qrf enqvngrhef nanybtvdhrf

Point Actionneur. Les actionneurs sont au point morts pour l'instant, ce n'est pas l'urgence.

Jeudi 12 Décembre

Y avait du monde

Point Mécanique. Le dossier github de le méca a été crée et actualisé, on attend les prolés.

Point Phare. Le phare est en cours d'impression cela va prendre plusieurs jours.

Point Puissance. Le code de contrôle des moteurs a été conçu par Emile. L'utilisation de deux ponts en

H (LMD18200) est actée. Les moteurs fonctionnent en 16V ils seront donc directement mis sur la batterie. La

communication entre Ptit Lu et Martin est faite.

Point Asservissement. L'idée est plutot d'attendre Clément et son expérience. Emile a testé les deux mo-

teurs ils sont bons, les encodeurs sont en cours de test. Grâce à Matthieu, Emile arrive à utiliser la Nucléo. Le

code a été commencé, Liam rééchit à la théorie de manière assez poussée.

Point Informatique. Grâce à OpenClassRoom Sébastien sait faire du C++ (enn en théorie). L'algorithme

de recherche de chemin est semi-implémenté grâce au projet ours. L'interface du robot n'a pas commencé.

Point Alimentation. Ptit Lu a dit : Mangez 5 fruits et légumes, c'est bon pour la santé. Le rootage de

la carte doit débuter ce soir et on met pas de radiateur pour faire en sorte que le robot ait plus de chance de

bruler. Le récapitulatif du schéma électrique est disponible dans les descriptions.

Jeudi 16 Janvier

Point Mécanique. La base du robot a été découpé ce jeudi. Le montage devrait avoir lieu dans la semaine

Point Phare. Le phare est en cours d'impression cela va prendre plusieurs jours. Mais il est stylé de ouf.

Point Puissance. Le design est fait à priori.

Point Asservissement. Retour de Clément ! Il a fabriqué un banc de test et commencer à tester quelques

codes. Alban a dispensé une petite formation sur mbed pour les aider.

Point Informatique. Discussions sur le protocole de communication entre la Raspberry Pi et la Nucléo.

Utilisation d'une liaison série (via USB sûrement). Présentation des avancements de la stratégie et schéma

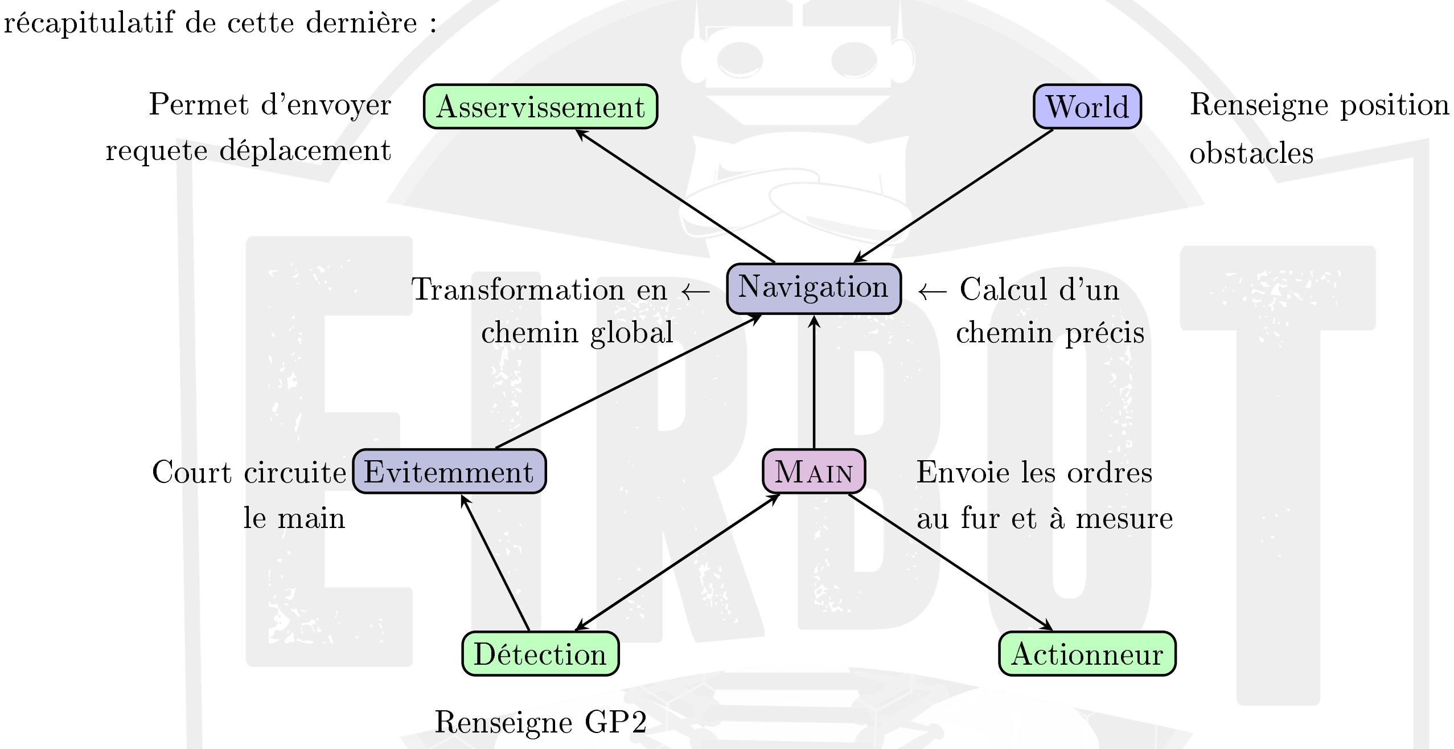
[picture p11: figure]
récapitulatif de cette dernière :; Main; Envoie les ordres; au fur et à mesure; Navigation ← Calcul d'un chemin précis; Transformation en ← chemin global; World; Renseigne position; obstacles; Permet d'envoyer; Asservissement; requete déplacement; Court circuite Evitemment le main; Détection; Renseigne GP2; Actionneur

Achage

Point Alimentation. La 3ème tentative de fabrication de la carte d'alimentation a réussie (L'auteur de ce

rapport en a quand même raté deux :)) ! Perçage ni et soudures nies jeudi soir.

Jeudi 23 Janvier

(C'est mon anniversaire quand je tape se rapport, vous vous en foutez mais bon :'), en plus vous comprennez

pas qui est l'auteur, une fois Ptit Lu, une fois moi, on est perdu)

Point Mécanique. La découpe laser est cassée, Erwann devrait continuer la modélisation des étages

Point Alimentation. La carte est nie, il faut tester la carte et surtout penser aux cables , la gestion des

cables devrait être gérée par Julien.

Point Puissance. Martin n'a plus qu'à les imprimer (peut être aidé par Julien) il faut vérier l'empreinte

des composants.

Point asservissement. Liam a commencé le codage et la création des classes, on a plutot tapé sur le haut

niveau, il manque le traitement des données par Clément. Emile a crée une conversation messenger (preuve de

son utilité moindre)

Point protocole de com. (pourquoi c'est pas toi qui tape ce rapport ?) Le protocole est TRES bien avancé,

on peut envoyer et recevoir des données mais ça beug un peu

Point actionneur. Filipe a travaillé ! ! (il a fait un pignon on se chaue pas trop non plus)

Point phare. (Il est beau ! !) On a imprimé 6 pièces sur 7 , il faut encore créer la carte d'alimentation

Point information. Il y a eu un peu de changement dans le principe, maintenant lors d'une requete de

déplacement l'asserv peut renvoyer : ok, timeout ou detection cela a permis de fusionner facilement la

détection et la navigation.

Point compteur. On a compris qu'il fallait compter les points, julien s'en occupe.

Jeudi 6 Février

C'est le première réunion en salle de réunion, c'était sympa

Point Mécanique. A cause de la panne de la découpe laser les prolés n'ont pas pu être installé. On félicite

Erwann pour le défaut de conception sur les manches à Air :). Plusieurs objectifs ont été xé. Tout d'abbord

Erwann devrait concevoir les supports de GP2. Il commence aussi à réechir à la méthode de construction de

la balise.

Point Alimentation. Le cas général fonctionne très bien. Il faut encore tester les cas critiques et commencer

à les installer sur le robot.

Point Puissance. Martin et Filipe travaillent désormais ensemble. Ils se sont xés deux semaines pour sortir

une première version des cartes.

Point Shield. (Oui c'est un nouveau point) Yohann à réalisé une bonne partie de la conception, maintenant

il faut qu'il récupère les informations de tout le monde pour être sur de réaliser un shield précis. La quête des

informations commence.

Point Asservissement. Il a passé 3 heures à installer MatLab, malgrès sa modestie l'asservissement avance

très bien. Le robot arrive à être commandé (sans faire n'importe quoi), Matthieu l'a aidé pour faire une méthode

de caractérisation des moteurs. Cela prend du temps mais il avance très bien.

Point Stratégie. Nous avons fait le lien entre la stratégie et le protocole de Communication, actuellement

lorsque la stratégie envoie une requête à la nucléo, la requête est très bien envoyée et le retour est pour l'instant

générique.

Point Nucléo. Il faut réalisrr le cahier des charges pour Liam, il devra gérer les GP2 (activation / desacti-

vation, gérer la récupération des informations ), gérer les contacteurs et les actionneurs.

Point Phare. IL EST BEAU ! ! ! Il manque une pièce (le haut du phare), il reste à faire le circuit imprimé et

la communication avec le robot (433MHz).

Point Compteur. Julien connait la datasheet par coeur, et le schéma a été commencé sur Kicad.

Global. L'organisation physique du robot a été pensé.

Jeudi 13 Février

Point Mécanique. La découpe laser est réparée ! ! Le porte batterie est modélisé et en cours d'impression.

Les prolés vont pouvoir être installé sous peu et les supports GP2 ne sont pas commencés.

Point Alimentation. NON.

Point Puissance. Conception commencée.

Point Shield. Il a commencé la conception mais il attend que l'on soit sur de tous les pins etc.

Point Asservissement. Clément a pratiqué Matlab et il a trouvé les équations il faut encore faire les réglages

du correcteur

Point Stratégie. Il faut encore changer quelques trucs (comme la prise en compte de la distance pour les

obstacles)

Point Nucléo. La réunion avec Liam a été eectuée, le travail reste à faire

Point Phare. Une solution pour l'éclairage a été trouvé, avec une led 1W et un système de miroir comme un

phare réel.

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

Jeudi 27 Février

Point Mécanique. Clément : la méca c'est de la merde il y a un problème dans l'engrenage, dans les

moteurs, faire en sorte de ne pas avoir une vibration trop grande, il faut refaire le premier étage.

Point Asservissement. L'asservissement en vitesse de chaque moteur est plutôt bonne. Il faut maintenant

penser à un asservissement central par rapport aux deux moteurs et non par rapport à chaque moteur.

Point Alimentation. Il faut rajouter un fusible et voir la longueur des cables.

Point Phare. Marius attend l'arrivée des leds (il est beau le phare)

Point Communication. On verra plus tard, ta gueule sèb

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

Jeudi 12 Mars

Point Mécanique.

bloc moteur : avec nans pendant les vacances, ils ont fait un piece et elle est mieux que Hugo.

Est ce qu'on refait la base ? Le modele d3D est fait , Si clément se chaue pour refaire les trucs ça peut

être pas mal. Pas commencé support GP2, mais d'abord les étages

Point Alimentation. Les fusibles ont été rajoutés mais Nans est un tocard. C'est quand qu'on la monte ? Je

comprend pas tout quand les élecs parlent.

Point Puissance. On a fait cramer un pont en H (c'est 7 euros),si y a pas la coupe on peut transformer le

truc en table apéro.

Point Phare. On attend les LEDS

Point Asservissement. Il va bientot passer à l'asserv de position.

Point Nucléo. On s'amuse avec le bas niveau

Point détection. Commencer à étaloner le signal de sorti du GP2 parce qu'il fait de la merde.

Point Protocole. Il commence à faire le lien avec les diérents trucs.

Point Raspberry. ca marche c bon

Point Actionneurs. On va mettre 2 actionneurs en fait parce que c'est bien et seb galère avec des servo de

merde

Point compteur. J'ai rien branlé du compteur

Question 3A. ra snvg ba prafher çn wr fnvf cnf ?

En fait Nans parle. Du coup faut attendre 20h, mais en gros tous le monde commence à penser que y a

moyen que y ait pas de coupe, même on organise un mini eirbot chez Sèb, il a l'air chaud.
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

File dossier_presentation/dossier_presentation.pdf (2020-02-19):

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

Présentation des projets 2020 | 2
2 | Notre Projet

Cette année, Eirbot prend le large ! Nos robots doivent partir voguer à travers le monde. Nous allons

devoir maitriser la navigation pour arriver à bon port. C'est après une tempête qu'il faudra reconstruire le

chenal, réactiver le phare et redresser les manches à air pour espérer gagner. Nos robots évolurons sur la table

suivante

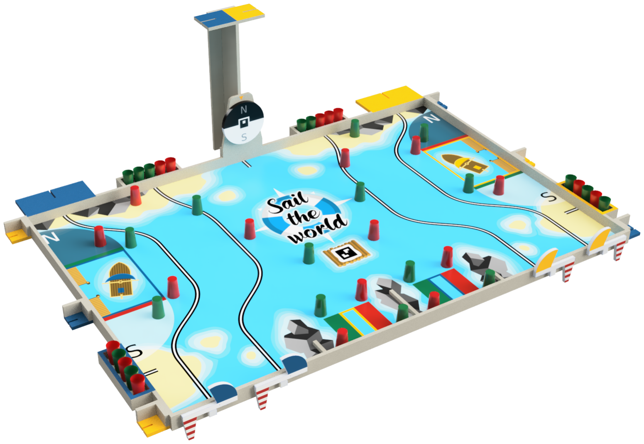
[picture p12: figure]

Figure 1 Schéma de la table de jeu

En plus de l'environnement de jeu nous devons suivre des règles précises disponibles sur ce lien. (https://www.coupederobotique.fr/wp-content/uploads/Eurobot2020_Rules_Cup_OFFICIAL_FR.pdf)

2.1 Vue d'ensemble du projet et objectif de l'association Voyons tout d'abbord l'objectif que nous allons nous xer pour ce projet. Nous avons décidé en commun

des diérentes actions et des diérentes tâches à réaliser. Nous décidons de réaliser les actions suivantes, activer

le phare, redresser les deux manches à air, décoder la boussole et retourner à bon port. Nous misons sur la

qualité des actions et non sur la quantité de ces dernières.

| Nous avons ensuite découvert le processus de fabrication d'un robot, grâce à l'aide des promotions supé-

rieures nous comprenons qu'il y aura 4 grands domaines : la mécanique du robot (la structure, les actionneurs,

le phare), l'électronique (alimentation du robot, contrôle des actionneurs, création du compteur de points etc),

l'asservissement (direction précise du robot) et la stratégie (recherche de chemin, choix des actions à faire etc).

2.2 Plans du robot Nous avons ensuite réalisé les plans de notre robot. Nous avons pu le rendre concret en majeur partie grâce

à la découpe laser du FabLab de l'ENSEIRB MATMECA et à notre imprimante 3D. En addition nous utilisons

des prolés pour monter la structure et créer des étages facile à monter et démonter.

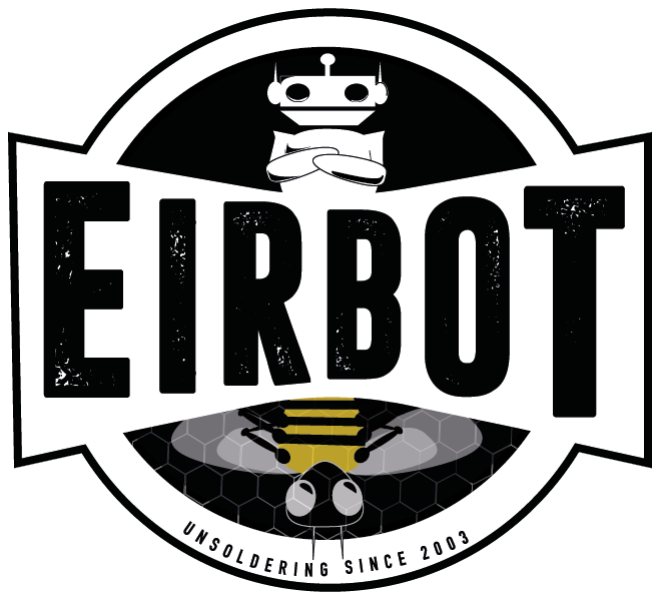
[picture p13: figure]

Figure 2 Photo de l'état actuel de notre robot

Concernant notre phare, il doit se deployer et réaliser un balayage lumineux (il doit faire moins de 30 cm

avant l'activation et plus de 70 cm après). Nous optons pour imprimer grâce à notre imprimante 3D un bras

robotique, le système d'éclairage de notre phare sera similaire à celui d'un vrai phare. Voici l'avancement actuel

de notre phare

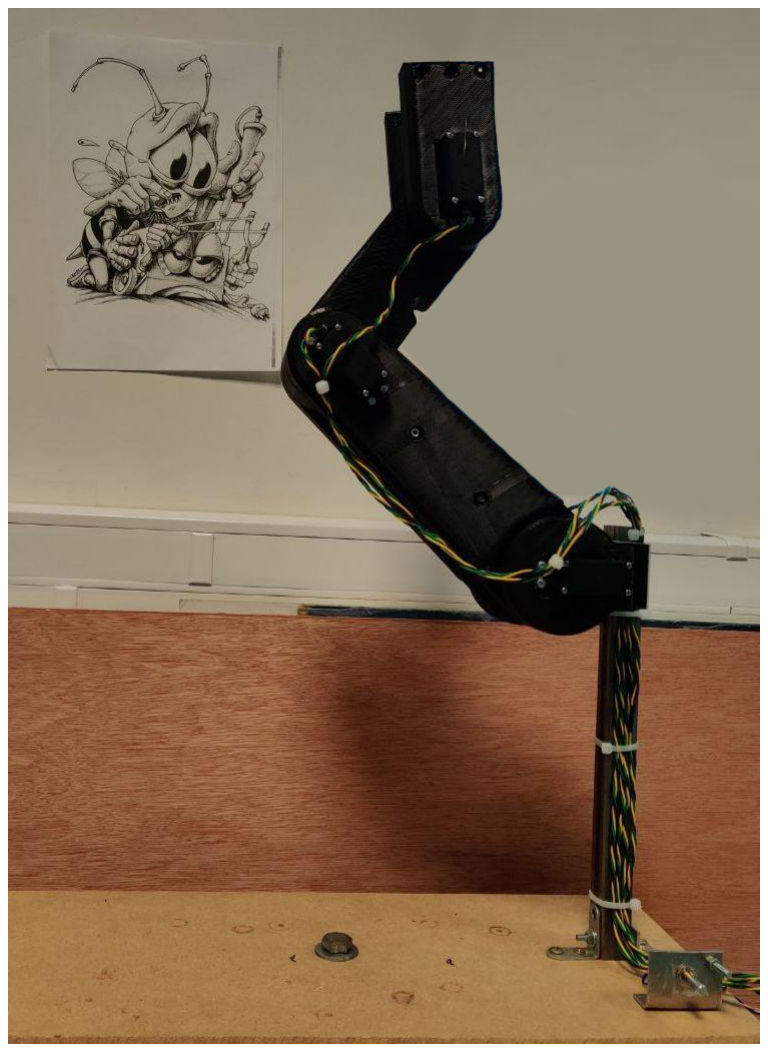
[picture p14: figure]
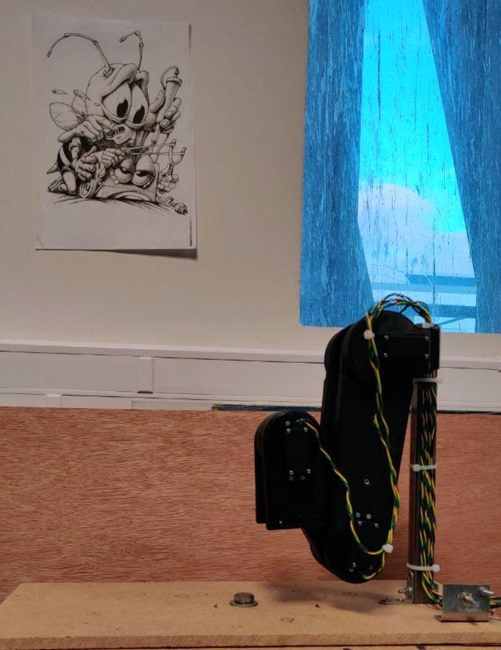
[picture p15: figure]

Figure 3 Photo de l'état actuel de notre phare replié Figure 4 Photo de l'état actuel de notre phare déplié

2.3 | Fonctionnement général du robot
| Comme dit précédemment nous misons sur la qualité de nos actions plutôt que la quantité. Nous divisons

alors le travail informatique en deux parties. D'une part l'Asservissement qui est implémenté sur une Nucléo-

F429ZI. D'autre part, la stratégie qui est implémentée sur une Raspberry pi 3b+. En addition nous avons du

créer un protocole de communication entre les deux cartes.

2.3.1 Asservissement

Nous pouvons commencer par décrire succinctement l'asservissement que nous avons élaboré

2.3.2 Stratégie

Nous pouvons maintenant décrire notre stratégie. La stratégie dépend de deux facteurs principaux, notre

capacité à naviguer sur la table et notre capacité à détecter les adversaires et à réagir lorsque nous tombons

face à l'un de.

Pour la navigation nous implémentons un algorithme de recherche de chemin connu dérivé de l'algorithme

de Dijikstra : l'algorithme A*. Nous décrivons rapidement son fonctionnement dans le paragraphe suivant, une

animation expliquant le principe de ce dernier est disponible sur ce lien. (https://fr.wikipedia.org/wiki/Algorithme_A*#/media/Fichier:Astar_progress_animation.gif)

Nous avons modélisé la table comme une grille chaque case faisant 1cm × 1cm. Ainsi nous avons pu

renseigner la position de tous les obstacles xes. A partir de cela nous pouvons expliquer le fonctionnement

de l'algorithme. l'A* commence à un noeud choisi. Il applique à ce dernier un cout initial, il estime ensuite la

distance entre ce noeud et le but à atteindre. Le noeud est alors ajouté à une liste d'attente prioritaire, appelée

open list.

Premièrement l'algorithme récupère le premier noeud de l'open list. Si elle est vide, il n'y a aucun chemin du

noeud initial à celui d'arrivé, l'algorithme est en erreur. Si le noeud est celui d'arrivé, l'algorithme va reconstruire

le chemin complet et renvoyer le résultat. Ensuite, si le noeud n'est pas le noeud d'arrivée alors de nouveaux

noeuds sont crées pour tous les noeuds contigus admissibles . L'A* calcule ensuite son coût et le stocke avec le

noeud. Ce coût est calculé à partir de la somme du coût de son ancêtre et du coût de l'opération pour atteindre

ce nouveau noeud. En parallèle l'algorithme conserve la liste des noeuds qui ont été vériés, c'est la closed list.

Si un noeud nouvellement produit est déjà dans cette liste avec un coût égal ou inférieur, on ne fait rien. Après,

l'évaluation de la distance du nouveau noeud au noeud d'arrivée est ajoutée au coût pour former l'heuristique

du noeud. Ce noeud est alors ajouté à la liste d'attente prioritaire, à moins qu'un noeud identique dans cette

liste ne possède déjà une heuristique inférieure ou égale. Une fois ces étapes eectuées pour chaque nouveau

noeud contigu, le noeud original pris de la le d'attente prioritaire est ajouté à la liste des noeuds vériés. Le

prochain noeud est alors retiré de la le d'attente prioritaire et le processus recommence.

Les détails technique des notre implémentation sont disponibles sur notre Github. (https://github.com/eirbot/eirbot2020-1A/blob/master/code/rasp/src/navigation.cpp) A ce stade, notre algo-

rithme est opérationnel et nous pouvons d'un point x, y donné rejoindre n'importe quel point x

0

, y⁰
en évitant

les obstacles xes. Nous allons maintenant présenter notre stratégie concernant les obstacles mobiles c'est à dire

les adversaires.

Nous utilisons un système infrarouge (GP2) pour la détection, ces derniers sont placés juste au dessus

des gobelets disposés sur la table (les gobelets sont considérés comme des obstacles xes, nous ne voulons

pas les détecter avec le système infrarouge). Lorsque nous détectons un robot adverse, la stratégie prend un

branchement, récupère l'information sur la distance que nous fournit le système infrarouge, ajoute un obstacle

puis relance la navigation ce qui permet d'éviter l'obstacle. A la n du branchement l'obstacle est détruit.

A ce stade nous pouvons avons un système de détection nous permettant d'éviter les robots adverses en les

contournants.

Nous avons présentés nos principales stratégies, nous n'avons pas décrit tous nos codes mais seulement les

principaux. Les autres codes sont disponibles sur notre dépot Github. (https://github.com/eirbot/eirbot2020-1A)

2.3.3 Protocole de communication

En choisissant de séparer sur deux cartes diérentes nos codes, nous avons une diculté supplémentaire

qui apparait. Il faut réaliser un protocole de communication entre les deux

2.4 Electronique du robot

## 3 Projets antérieurs

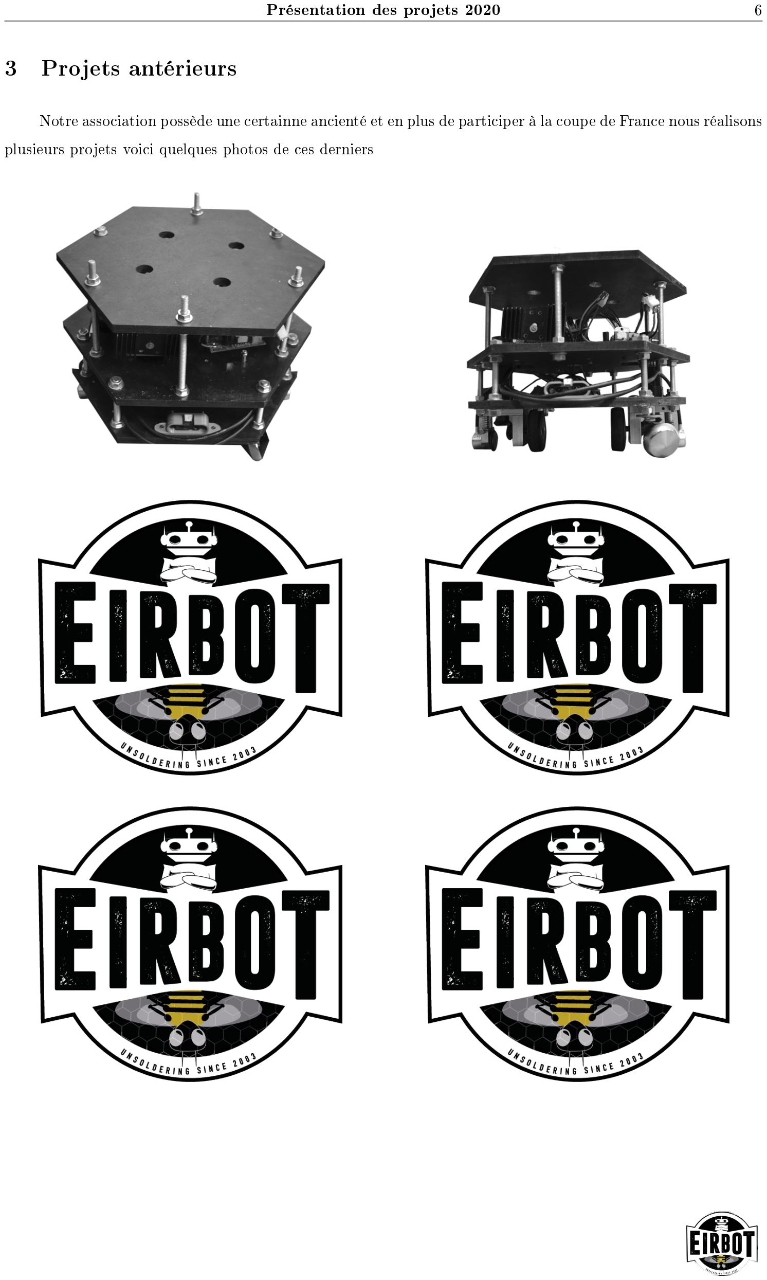
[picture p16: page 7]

Notre association possède une certainne ancienté et en plus de participer à la coupe de France nous réalisons

plusieurs projets voici quelques photos de ces derniers

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

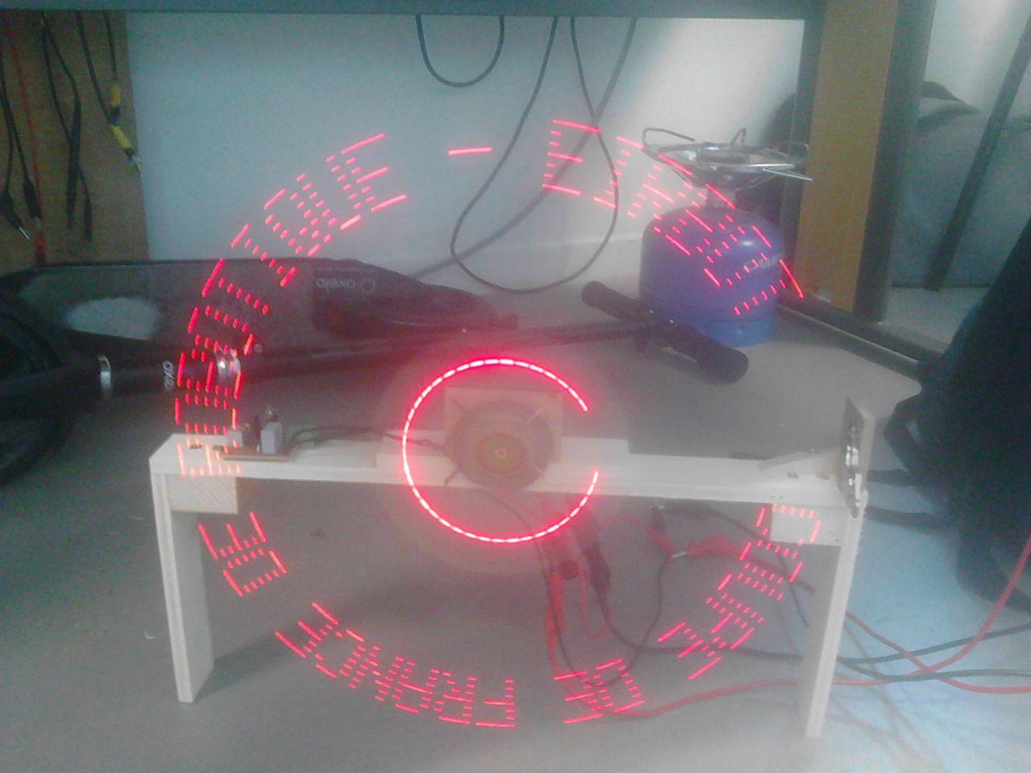
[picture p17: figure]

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

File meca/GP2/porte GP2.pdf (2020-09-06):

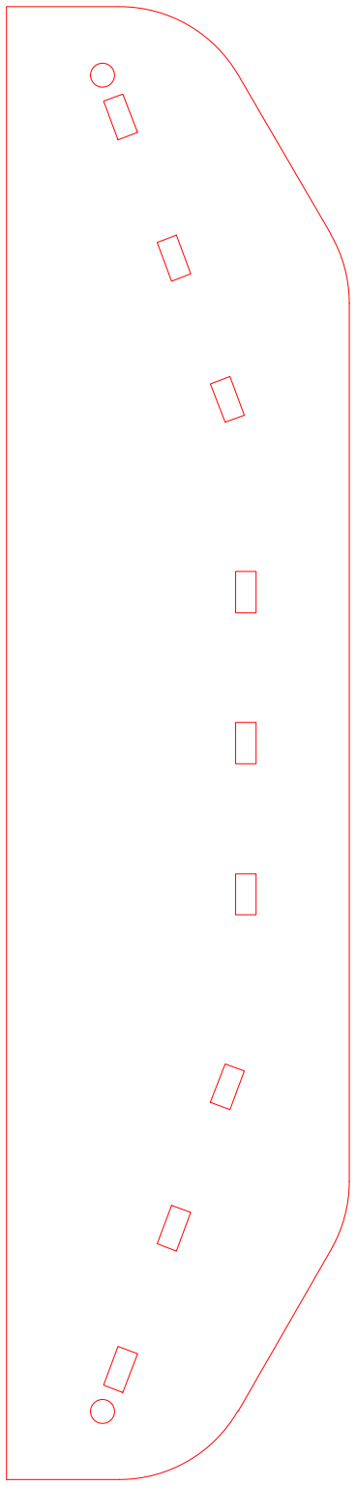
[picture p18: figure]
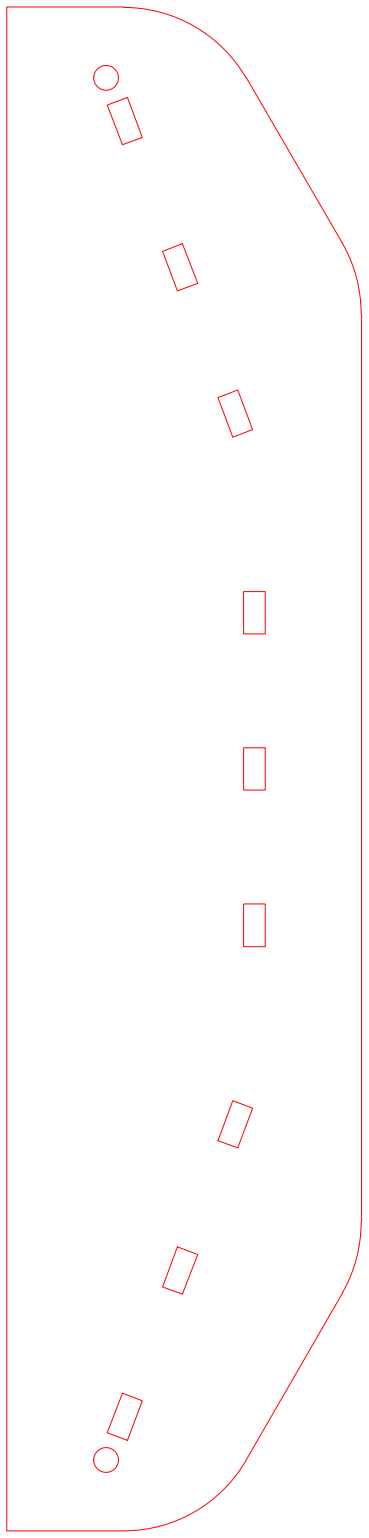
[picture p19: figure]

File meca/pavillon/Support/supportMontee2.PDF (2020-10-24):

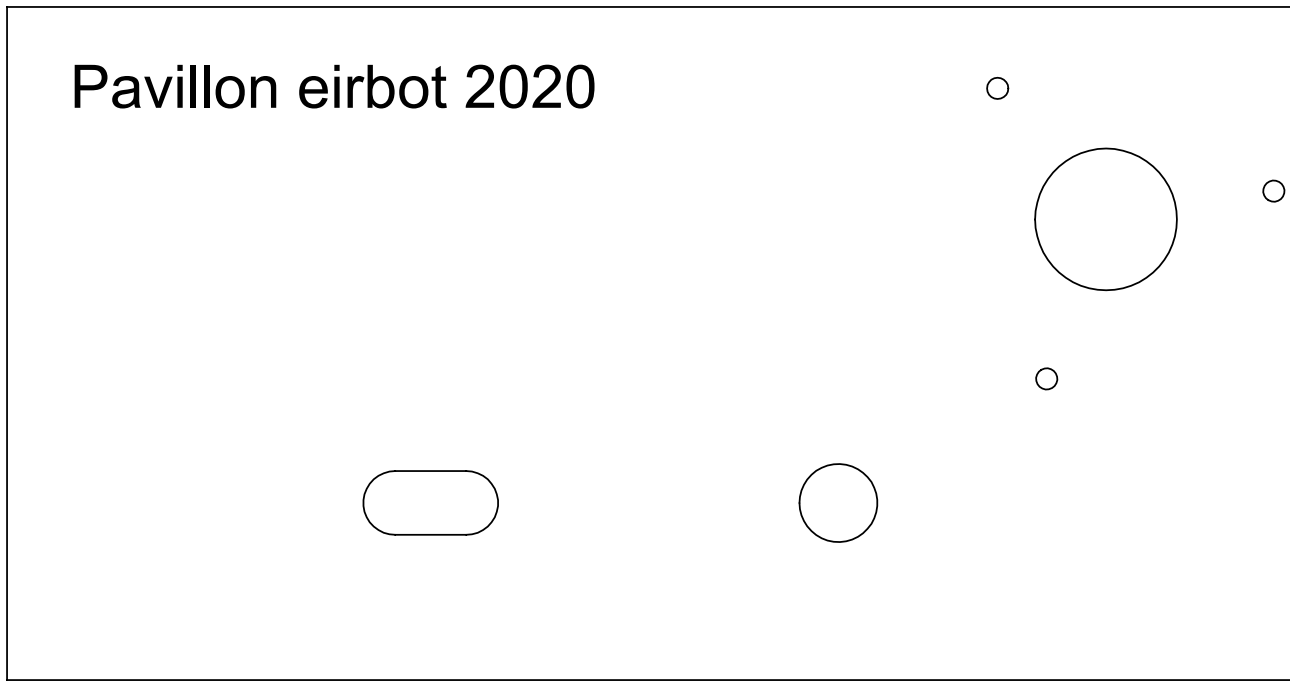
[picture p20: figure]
Pavillon eirbot 2020

Produit d'éducation SOLIDWORKS – A titre éducatif uniquement.

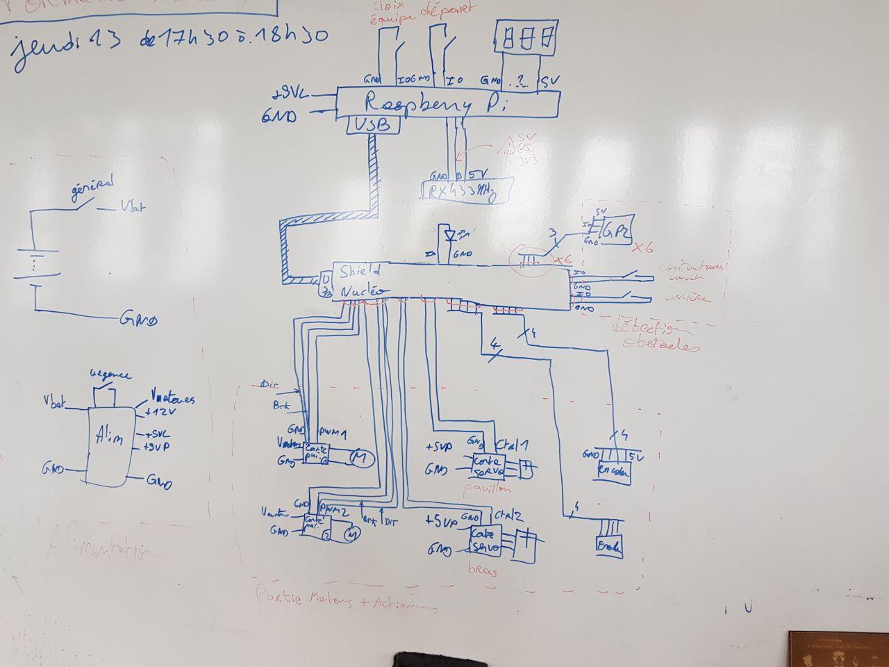
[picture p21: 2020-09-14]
alim/schema_global.jpg

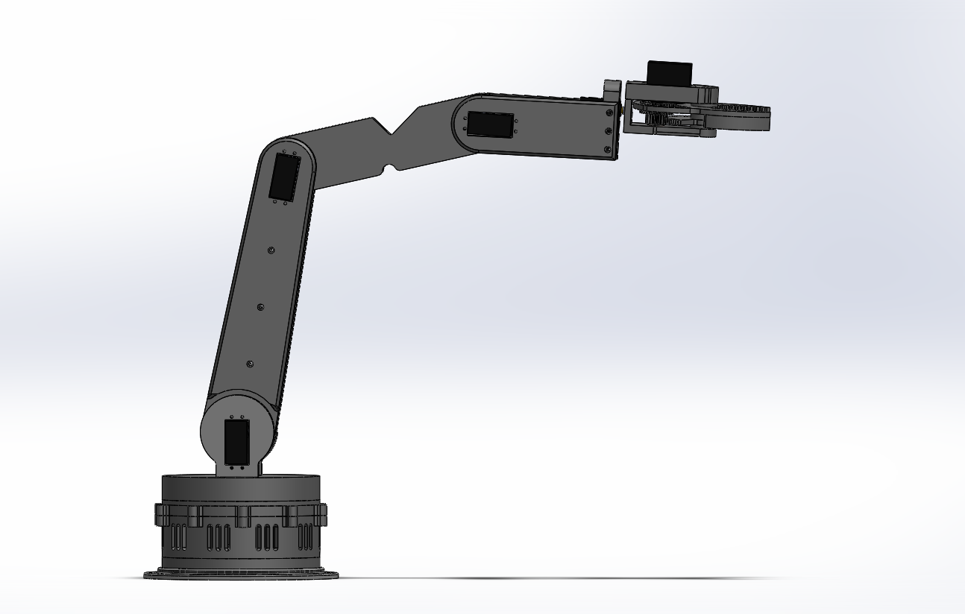
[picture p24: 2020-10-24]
meca/Phare/arm2.png

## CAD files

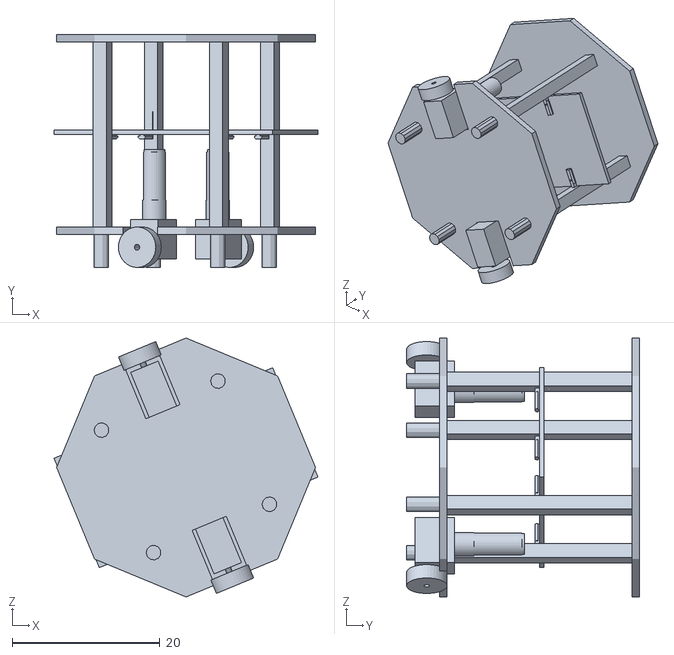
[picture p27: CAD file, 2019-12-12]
meca/robot/AssemblageV2.stl
35.7 x 31.5 x 35.0

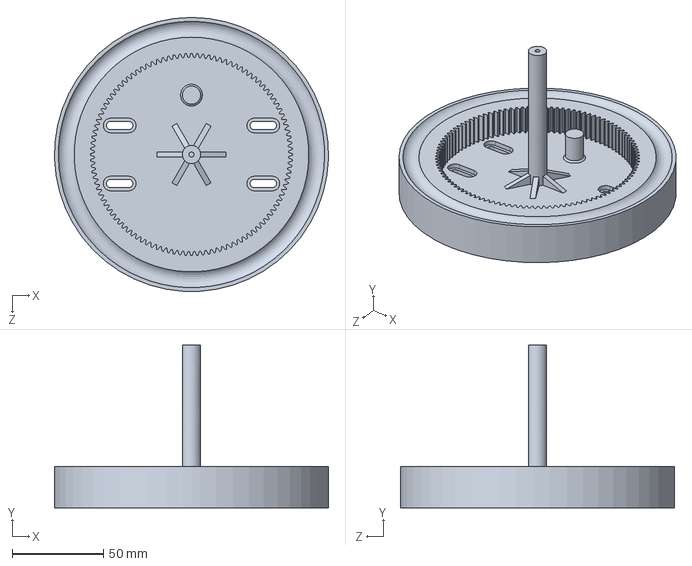
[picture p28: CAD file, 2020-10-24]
meca/Phare/A modif Phare/Rotating plate.SLDPRT
149.9 x 89.0 x 150.0 mm

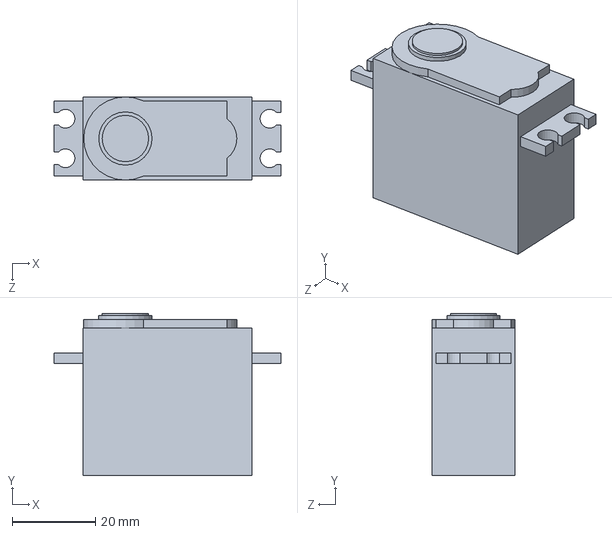
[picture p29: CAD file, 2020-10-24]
meca/Phare/MG996R/servo.SLDPRT
54.5 x 39.0 x 20.0 mm

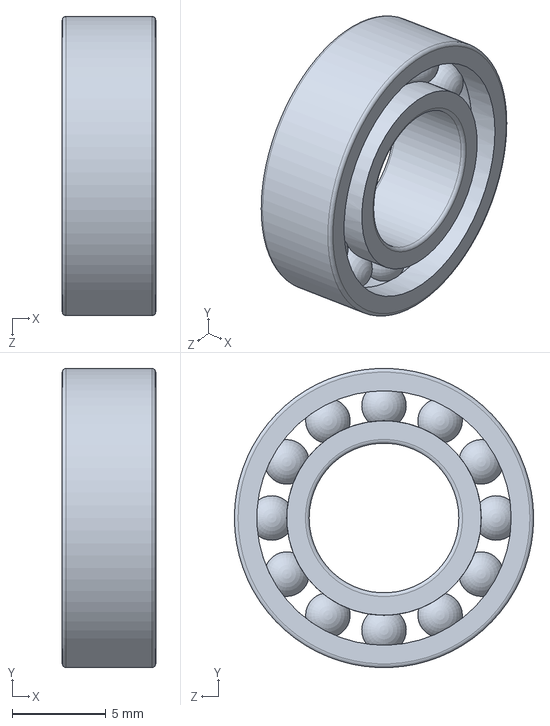
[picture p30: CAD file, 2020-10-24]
meca/Phare/sanal montaj malzemeleri/toptutucu.sldprt
5.00 x 16.0 x 16.0 mm

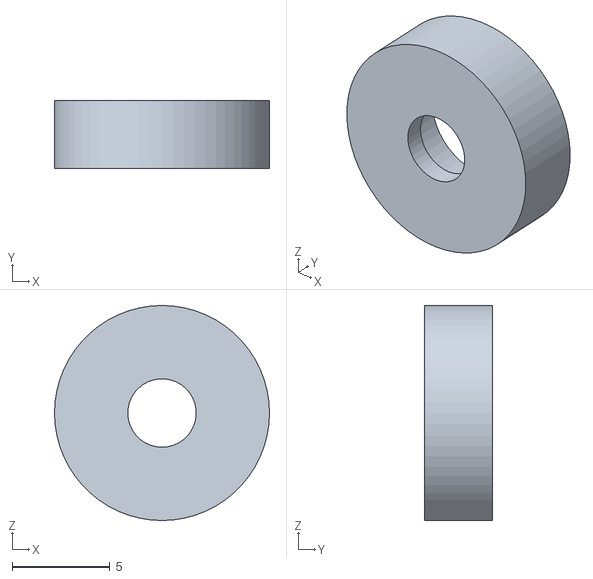
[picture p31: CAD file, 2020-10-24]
meca/Phare/slt Phare/Center arm bearing guide clamp.STL
11.0 x 3.50 x 11.0

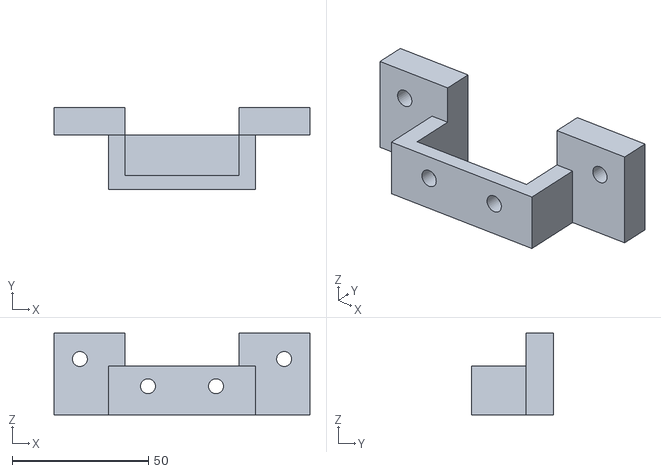
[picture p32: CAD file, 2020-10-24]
meca/robot/Support_Moteur_V2.stl
94.0 x 30.0 x 30.0

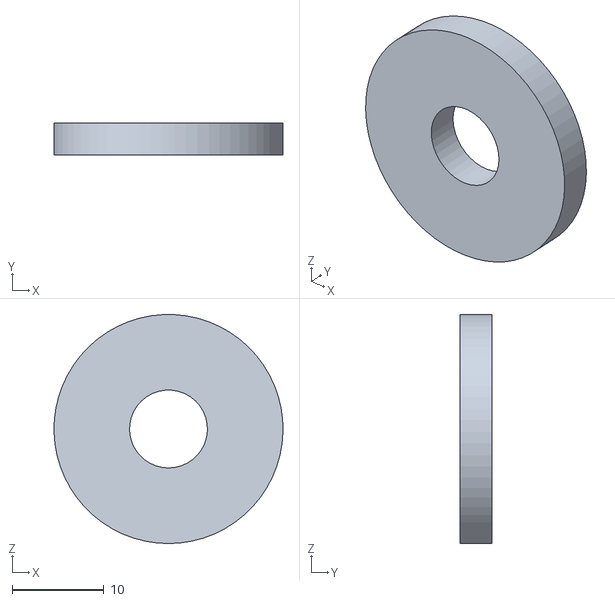
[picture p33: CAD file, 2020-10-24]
meca/Phare/kanca/files/stl/Bearing top-bottom bushing(2 defa basılacak).STL
25.0 x 3.50 x 25.0

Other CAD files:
meca/GP2/support GP2.dwg
meca/Phare/taban/files/Design_files/Rotating plate.SLDPRT
meca/Phare/taban/files/Design_files/stl/taban/Rotating plate.STL
meca/table/Ecueils/Temp.dwg
meca/Phare/MG996R/shaft.SLDPRT
meca/Phare/SLD Phare/Bearing holder.SLDPRT
meca/Phare/SLD Phare/Center arm bearing guide clamp.SLDPRT
meca/Phare/SLD Phare/Center arm bearing guide.SLDPRT
meca/Phare/SLD Phare/Center arm.SLDPRT
meca/Phare/SLD Phare/Lower arm bushing.SLDPRT
meca/Phare/SLD Phare/Lower arm left.SLDPRT
meca/Phare/SLD Phare/Lower arm right.SLDPRT
meca/Phare/SLD Phare/Tete.SLDPRT
meca/Phare/SLD Phare/TeteCapot.SLDPRT
meca/Phare/SLD Phare/TeteLED.SLDPRT
meca/Phare/SLD Phare/Upper arm left.SLDPRT
meca/Phare/SLD Phare/Upper arm right.SLDPRT
meca/Phare/SLD Phare/hub.SLDPRT
meca/Phare/kanca/files/Bearing center bushing.SLDPRT
meca/Phare/kanca/files/Bearing top-bottom bushing.SLDPRT
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

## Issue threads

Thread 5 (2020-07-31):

Créer les teeshirt de la coupe

Sdelpeuch, 2020-07-31:
- Proposition de logo par Antoine Pringalle (Informatique)
- Faire valider par Chapelle
- Faire devis chez Yann et comparer avec les autres

 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

Sdelpeuch, 2020-07-31:
Ajouter "CFR" sur le logo

Closed 2020-11-01.

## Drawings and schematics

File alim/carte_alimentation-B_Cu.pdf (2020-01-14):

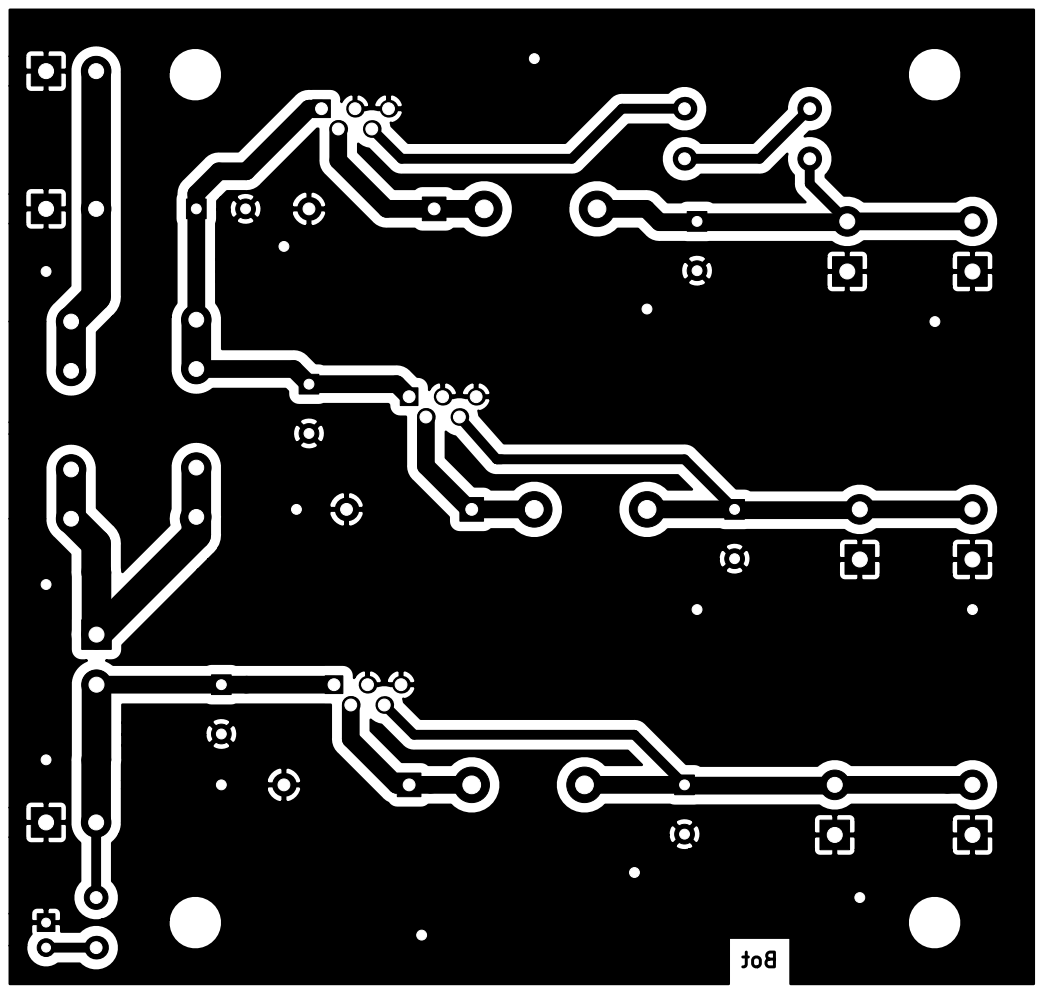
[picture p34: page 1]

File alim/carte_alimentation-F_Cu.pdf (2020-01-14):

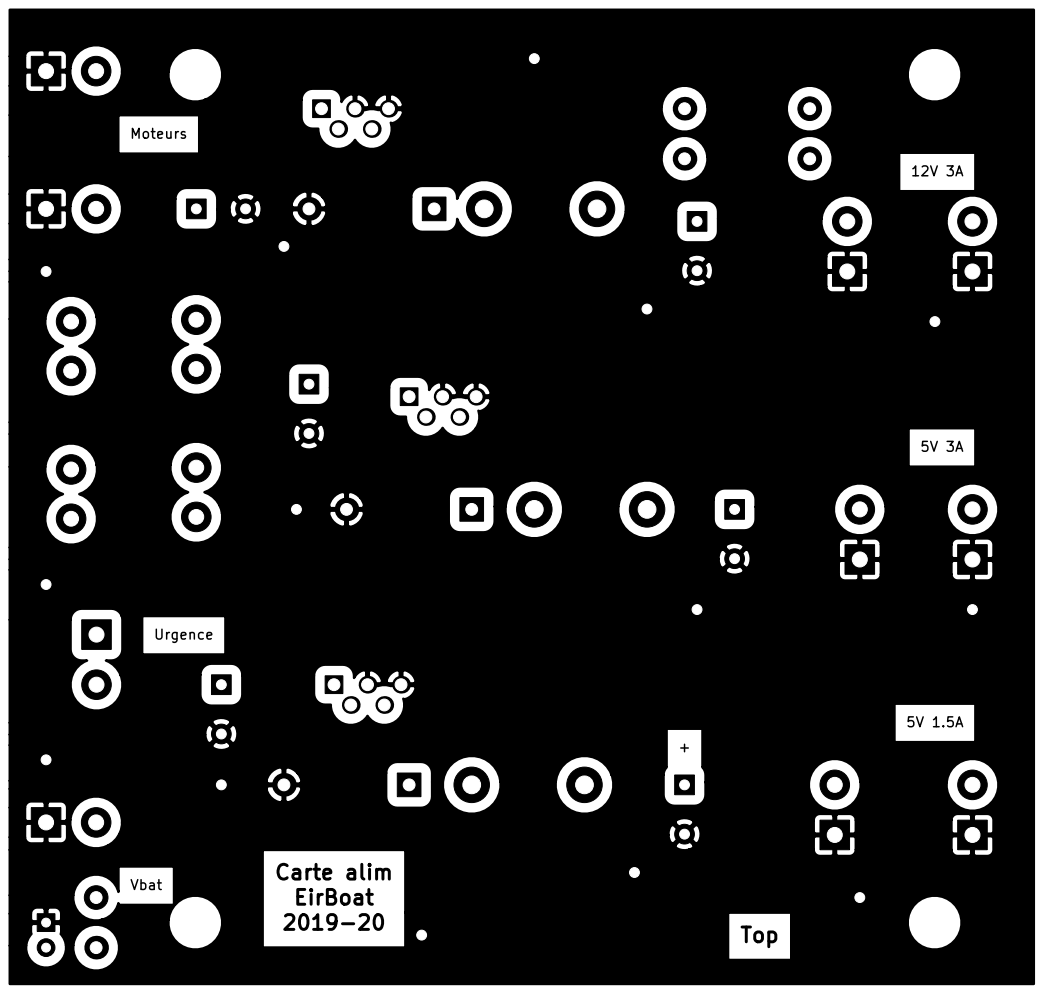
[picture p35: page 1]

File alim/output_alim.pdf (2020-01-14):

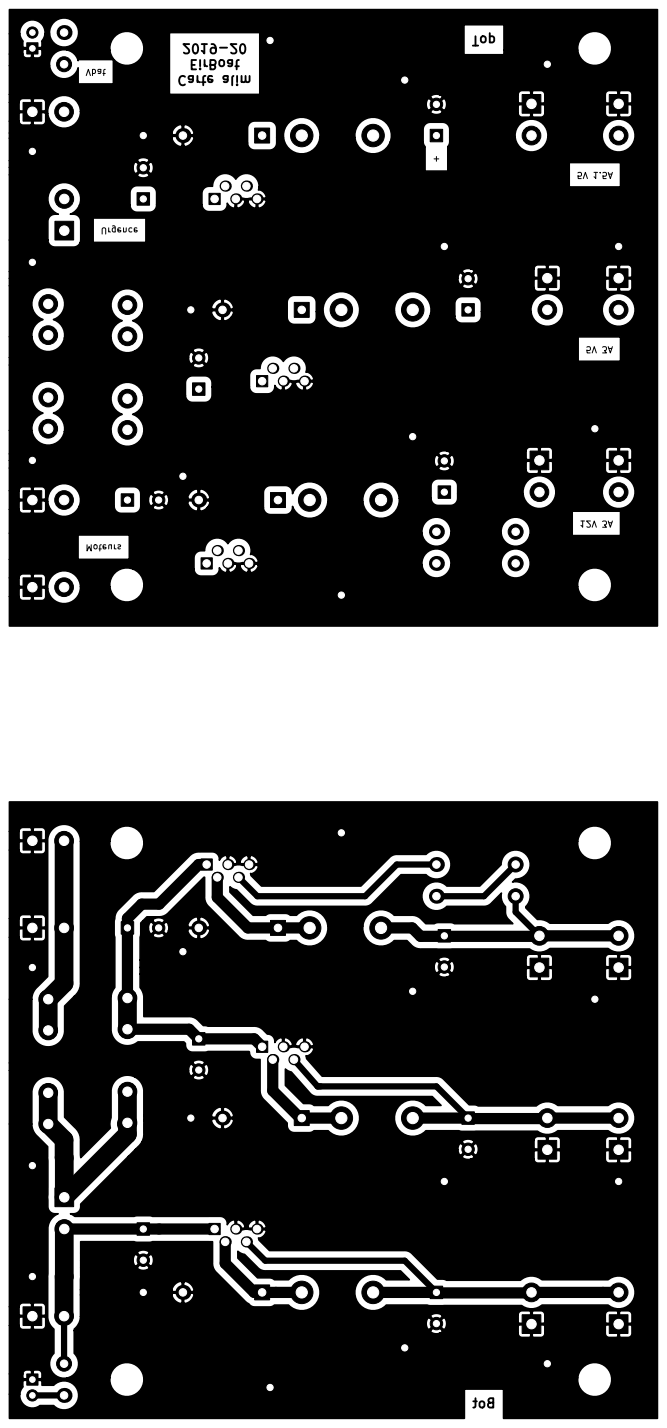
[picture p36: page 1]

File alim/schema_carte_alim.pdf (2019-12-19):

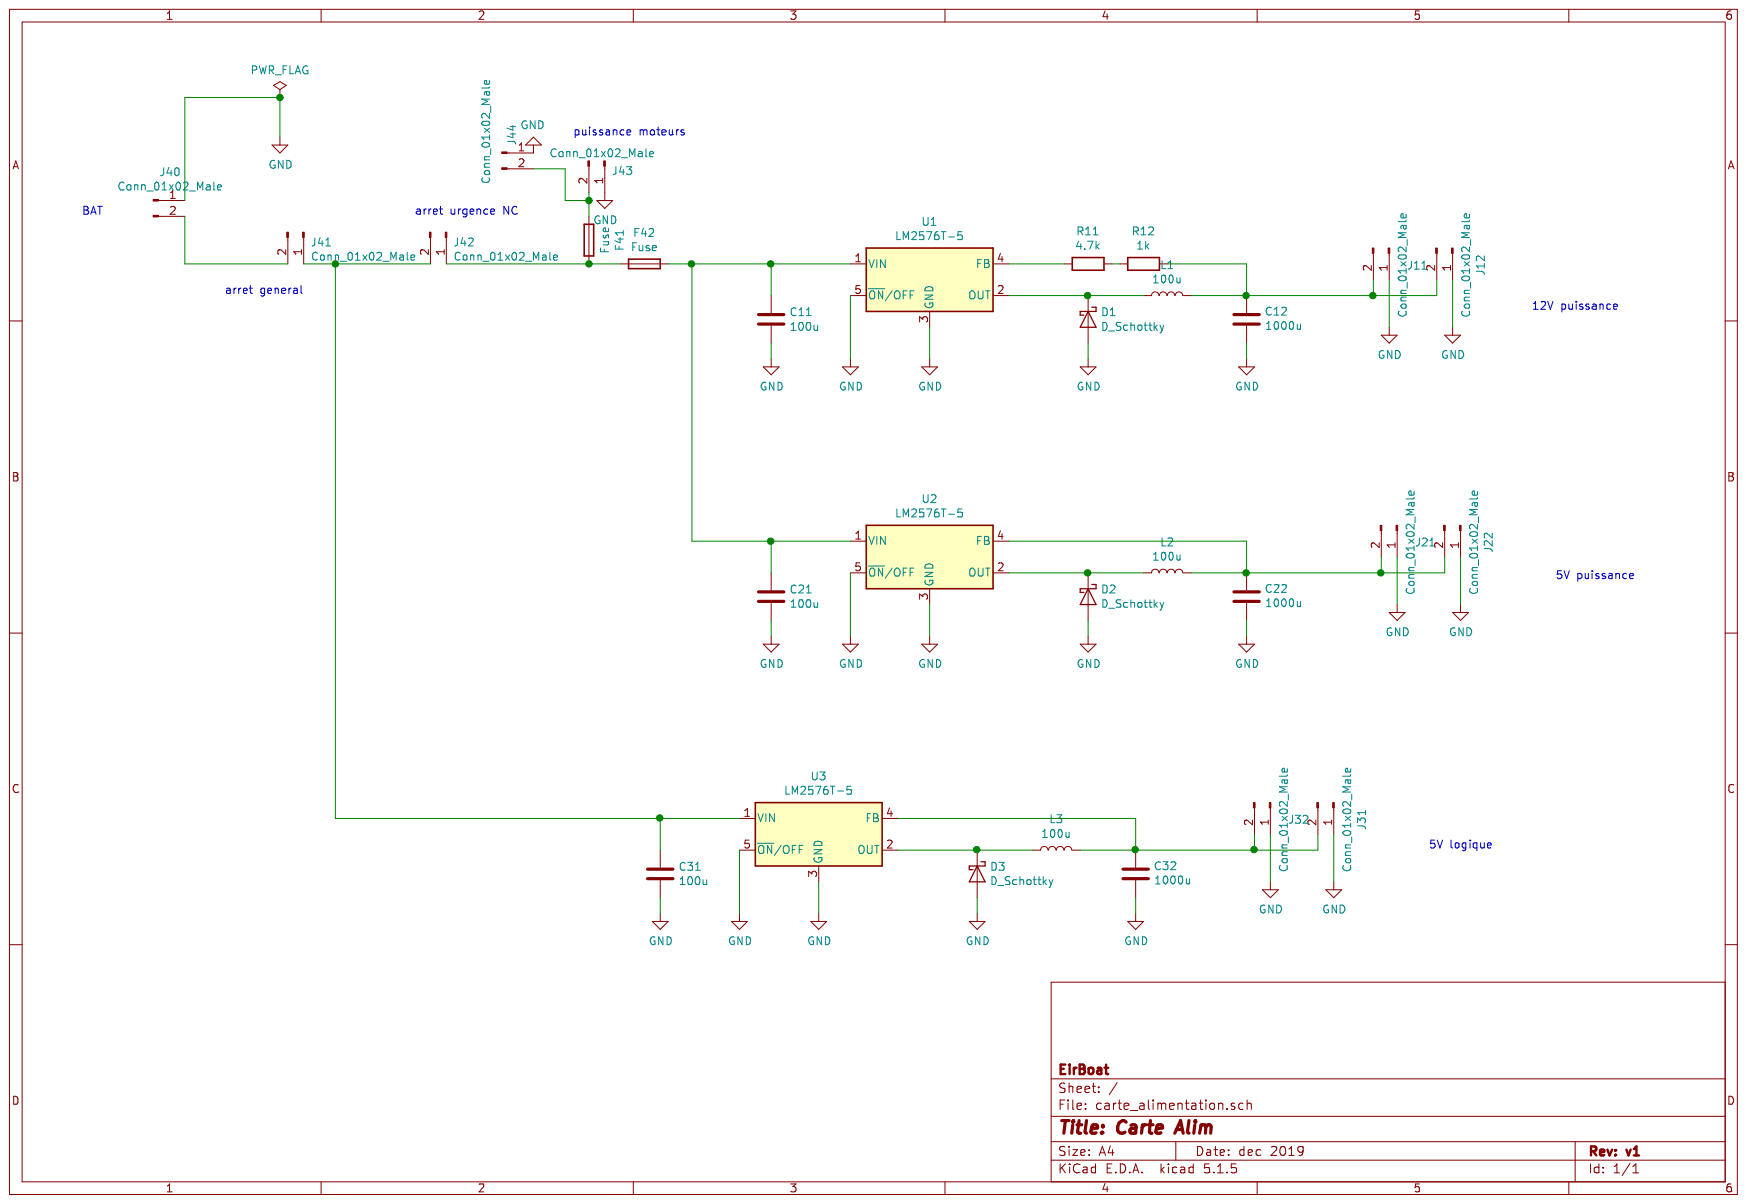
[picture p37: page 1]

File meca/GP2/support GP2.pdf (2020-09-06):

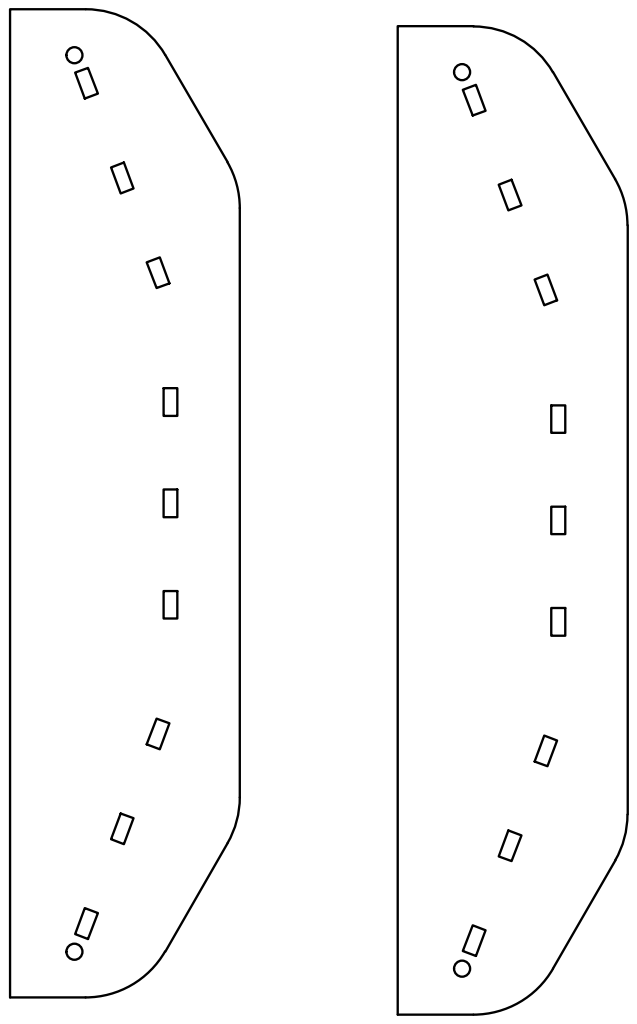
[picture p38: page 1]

DRAWN sebas | 03/09/2020

CHECKED

MFG

APPROVED

SIZE D | DWG NO | REV

SCALE 1 : 1 | | SHEET 1 OF 1

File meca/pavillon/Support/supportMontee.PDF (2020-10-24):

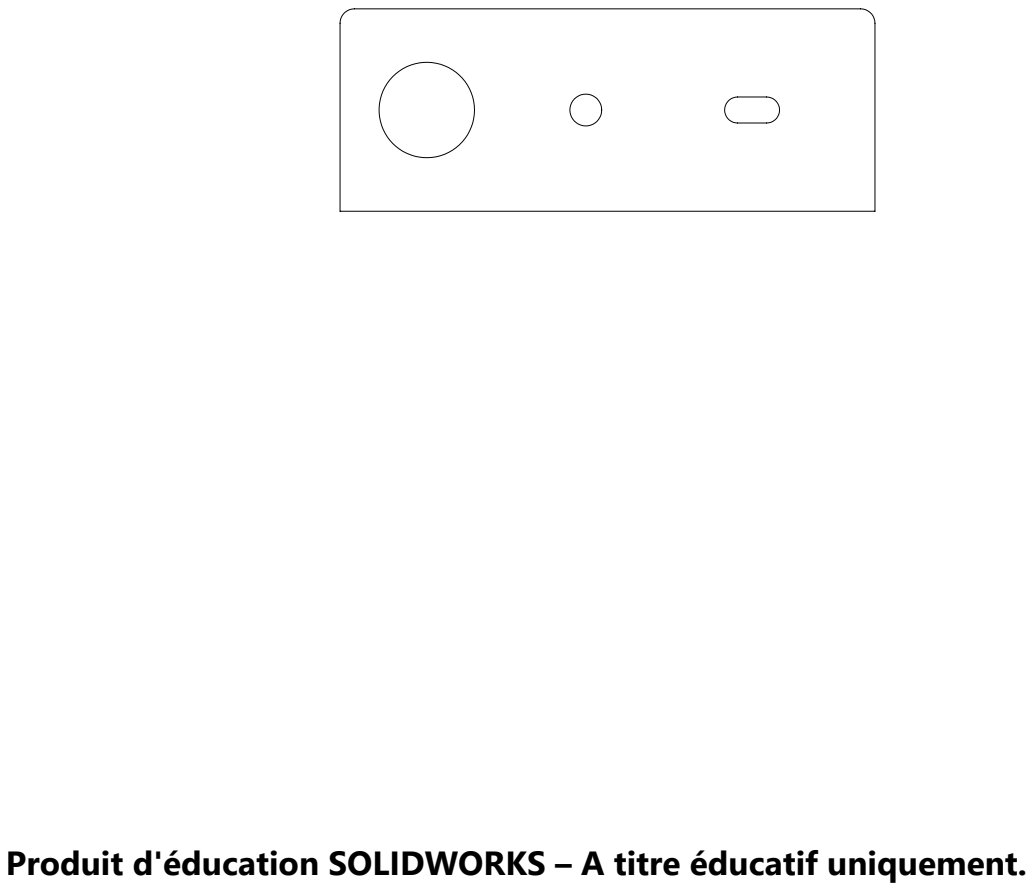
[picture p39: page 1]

Produit d'éducation SOLIDWORKS – A titre éducatif uniquement.

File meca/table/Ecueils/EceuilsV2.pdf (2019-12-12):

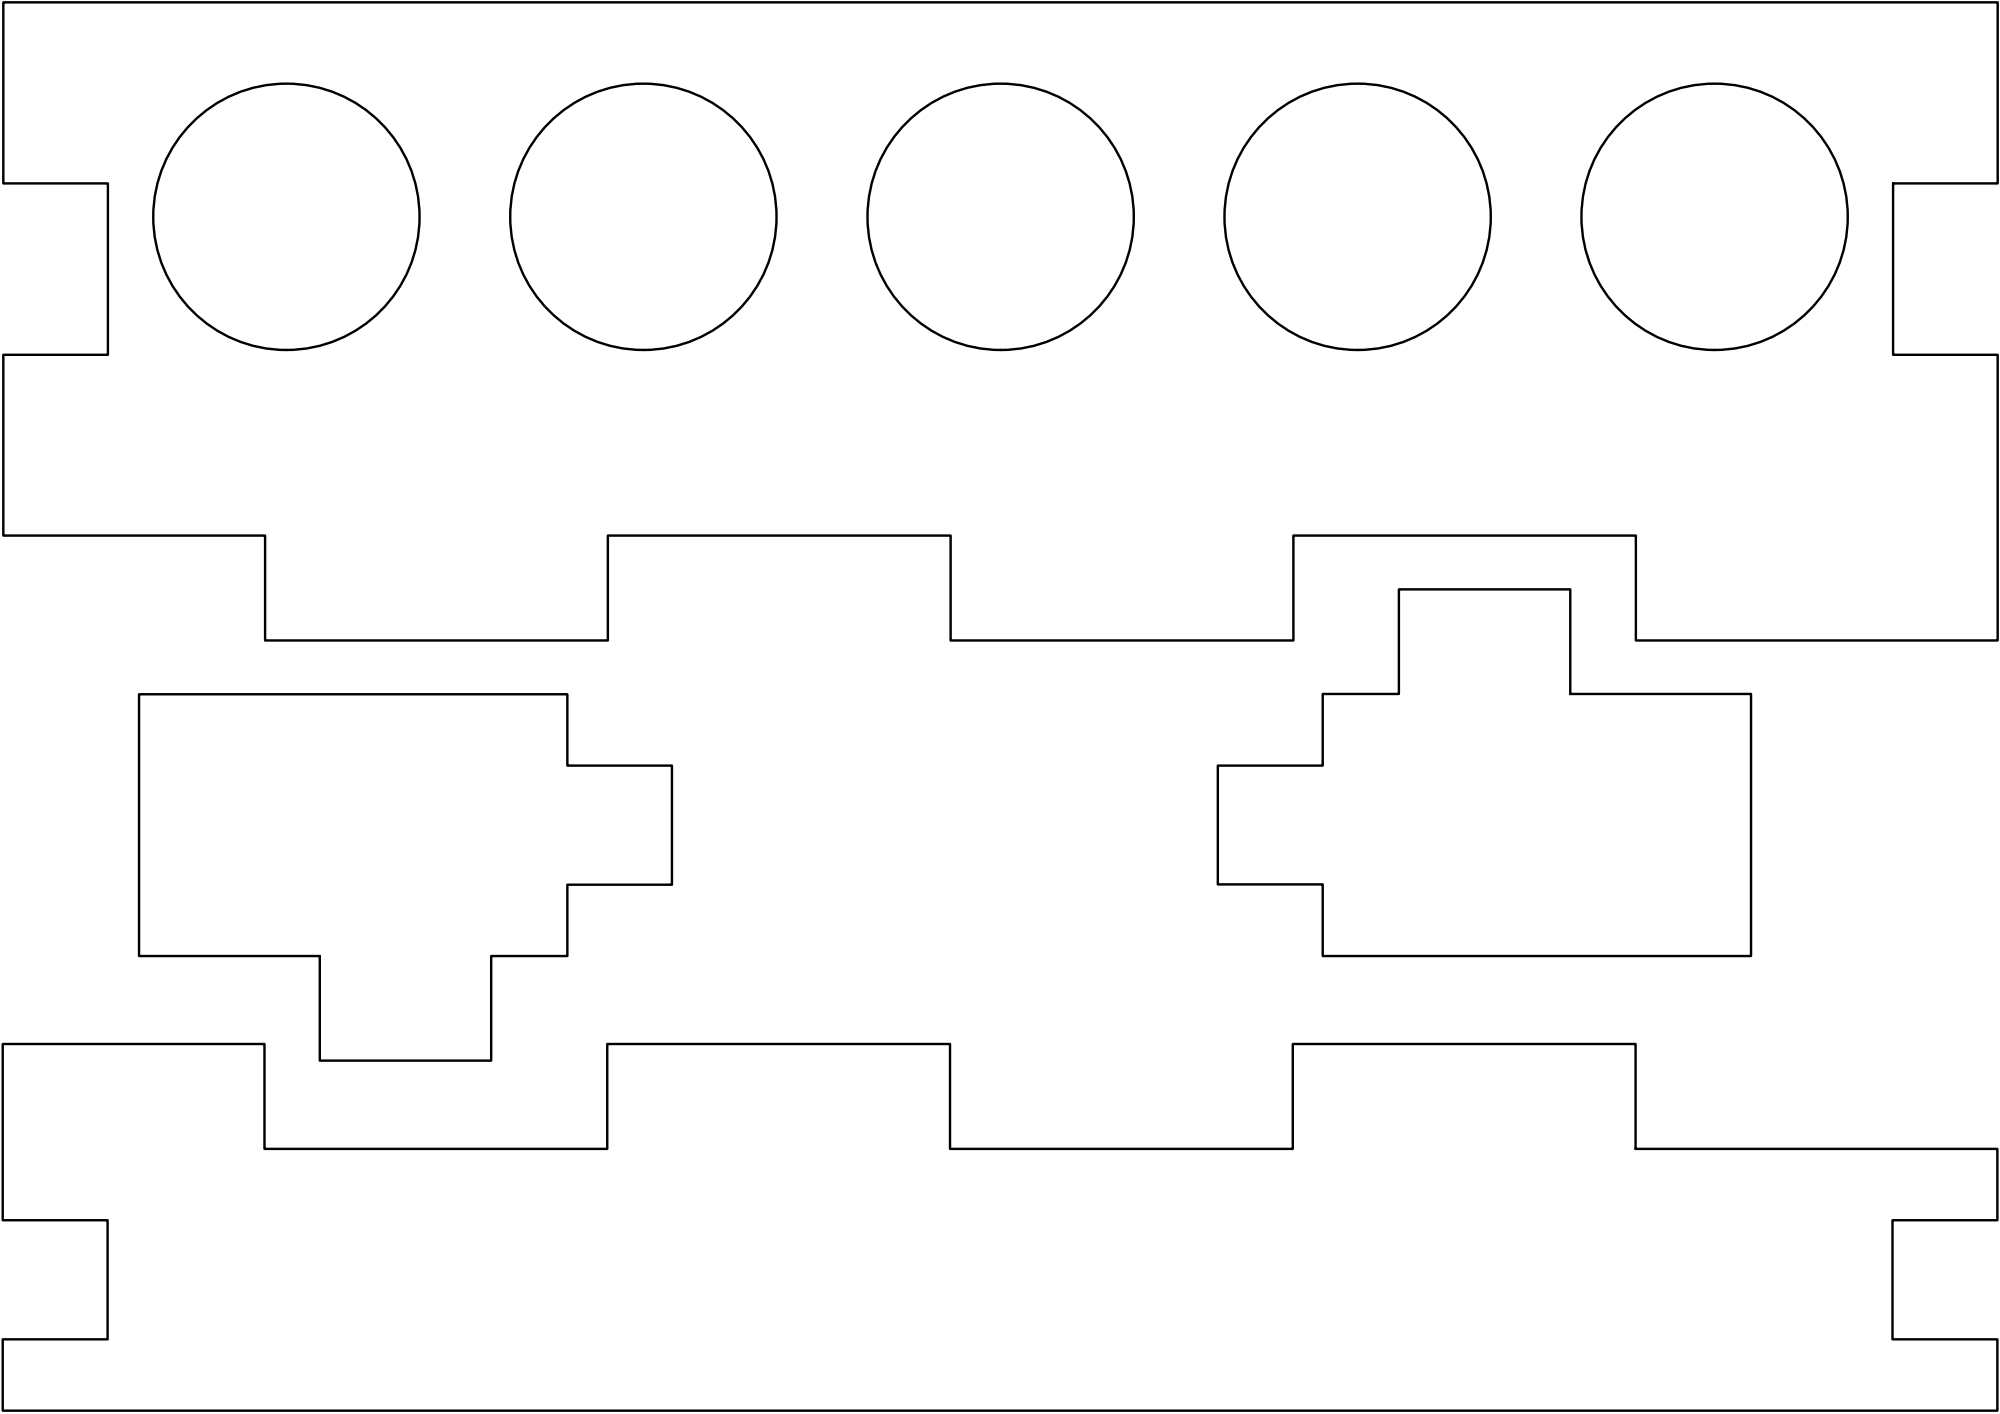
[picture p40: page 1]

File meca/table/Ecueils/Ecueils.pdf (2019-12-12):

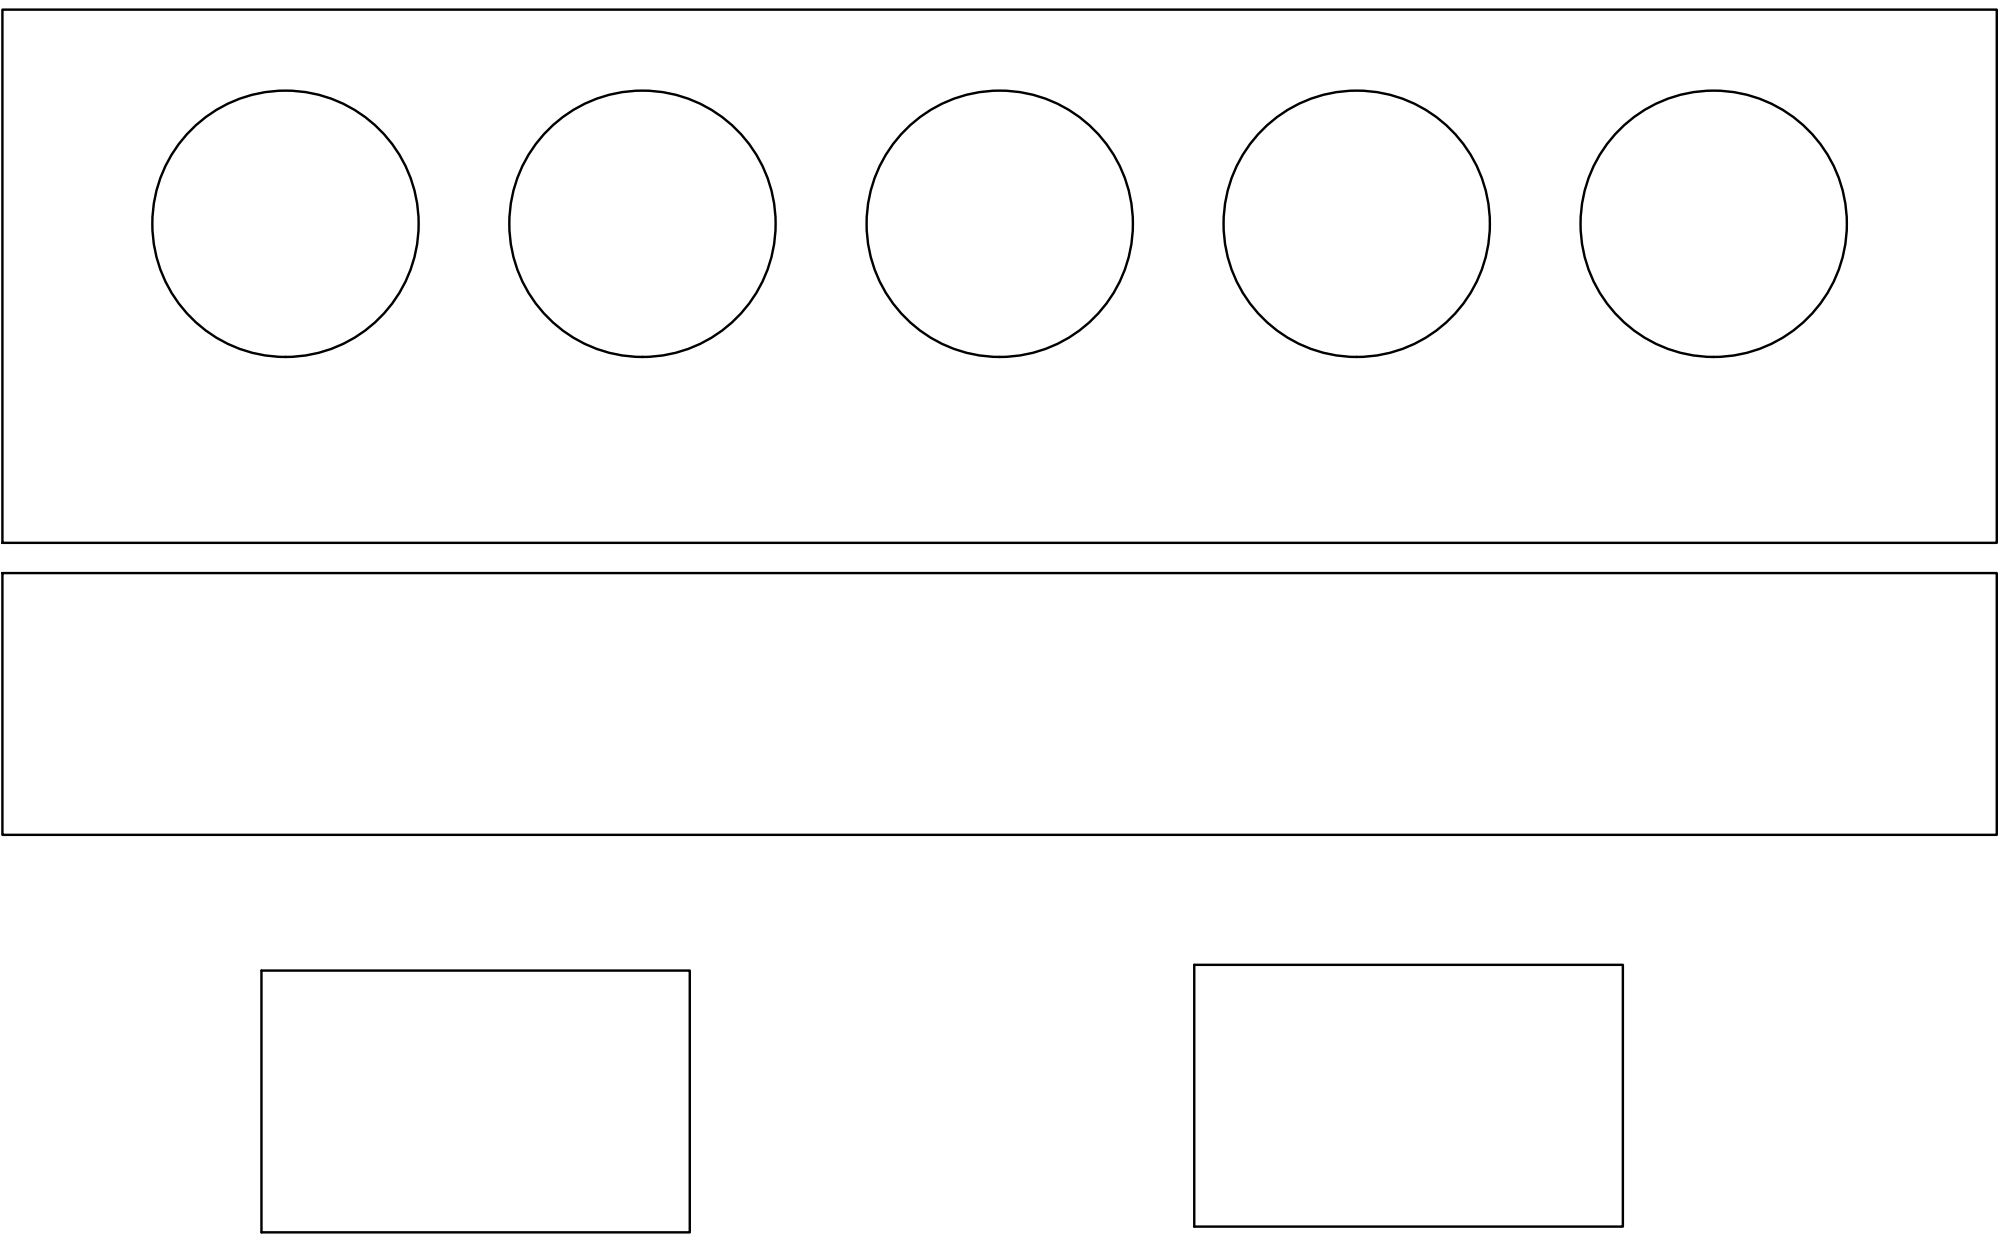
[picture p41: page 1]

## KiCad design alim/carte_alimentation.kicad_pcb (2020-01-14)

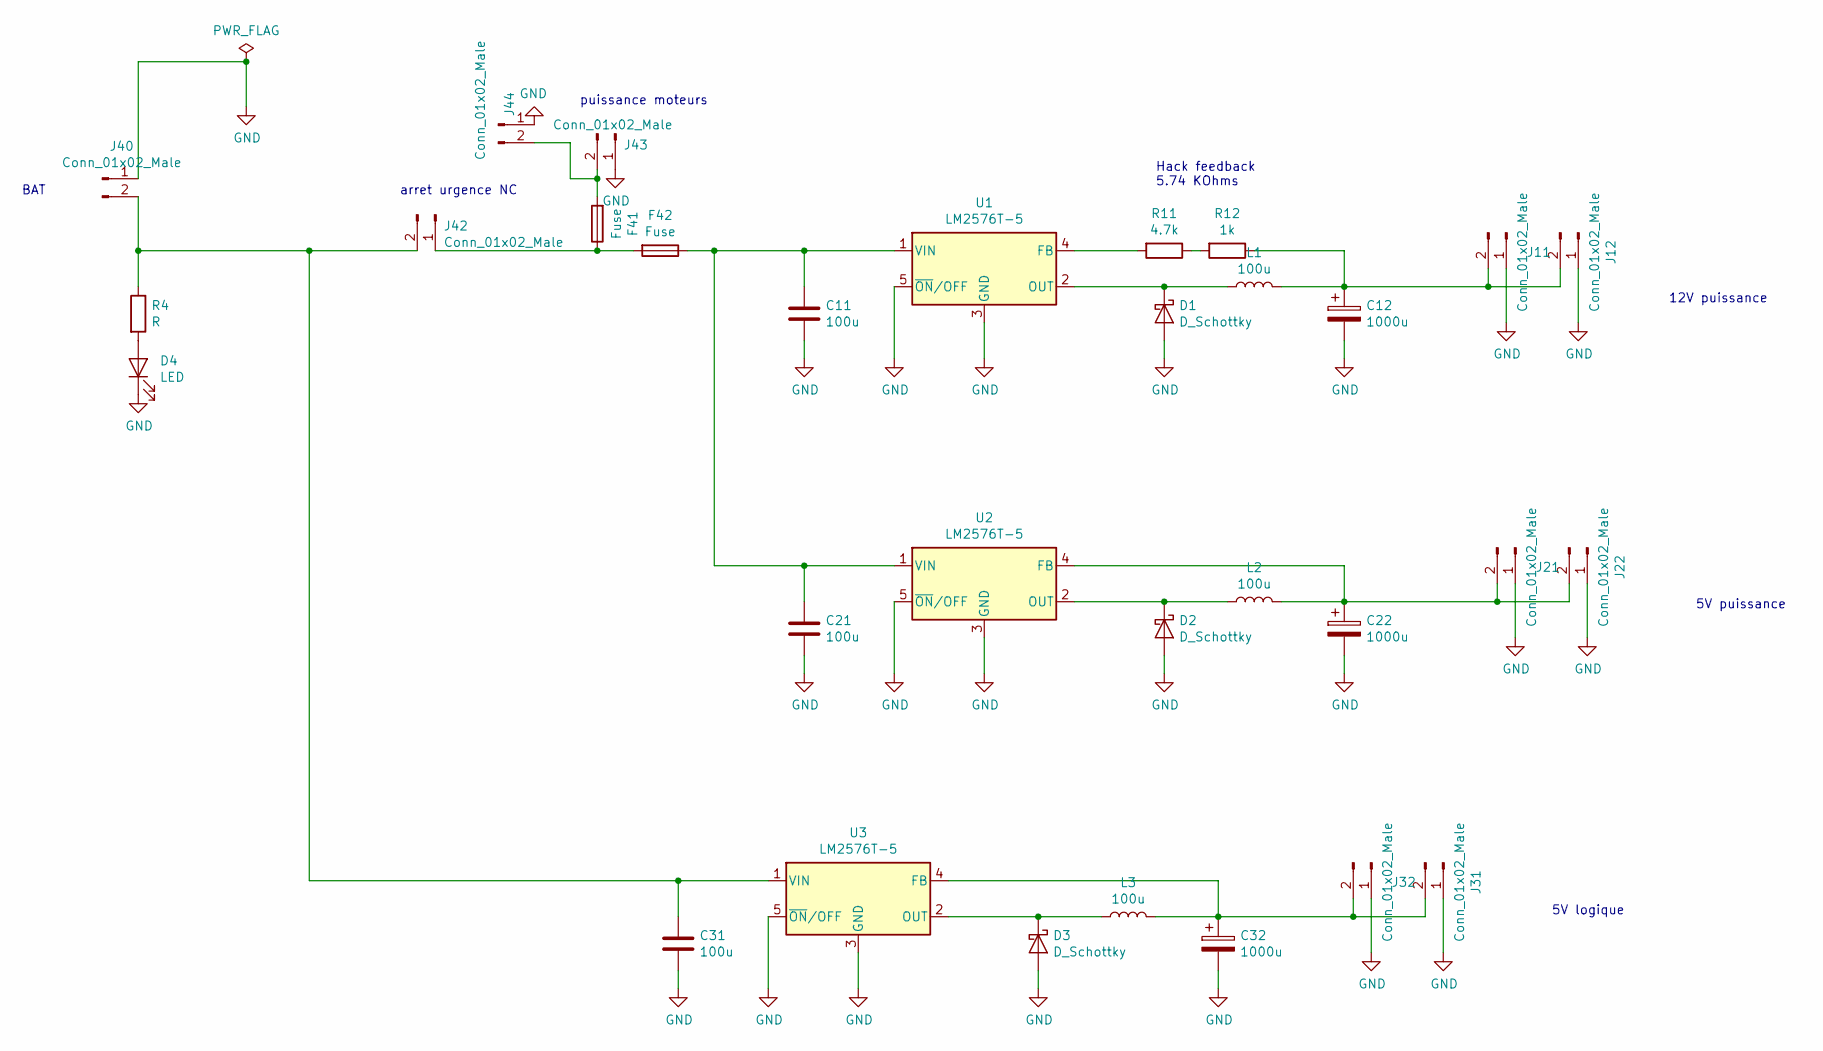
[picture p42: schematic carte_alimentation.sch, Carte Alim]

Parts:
C11, C21, C31: 100u; CP_Radial_D10.0mm_P5.00mm
C12, C22, C32: 1000u; CP_Radial_D10.0mm_P5.00mm
D1, D2, D3: D_Schottky; D_DO-27_P12.70mm_Horizontal
D4: LED; LED_D3.0mm
F41, F42: Fuse; fusible_alim
J11, J12, J21, J22, J31, J32, J40, J42, J43, J44: Conn_01x02_Male; TerminalBlock_bornier-2_P5.08mm
L1, L2, L3: 100u; L_Toroid_Vertical_L24.6mm_W15.5mm_P11.44mm_Pulse_KM-4
R4: R; R_Axial_DIN0411_L9.9mm_D3.6mm_P5.08mm_Vertical
R11: 4.7k; R_Axial_DIN0411_L9.9mm_D3.6mm_P12.70mm_Horizontal
R12: 1k; R_Axial_DIN0411_L9.9mm_D3.6mm_P12.70mm_Horizontal
U1, U2, U3: LM2576T-5; TO-220F-5_P3.4x2.06mm_StaggerEven_Lead1.86mm_Vertical

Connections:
GND: C11.2, C12.2, C21.2, C22.2, C31.2, C32.2, D1.2 (A), D2.2 (A), D3.2 (A), D4.1 (K), J11.1, J12.1, J21.1, J22.1, J31.1, J32.1, J40.1, J43.1, J44.1, U1.3 (GND), U1.5 (~ON~/OFF), U2.3 (GND), U2.5 (~ON~/OFF), U3.3 (GND), U3.5 (~ON~/OFF)
unnamed: C11.1, C21.1, F42.1, U1.1 (VIN), U2.1 (VIN)
unnamed: C12.1, J11.2, J12.2, L1.2, R12.1
unnamed: C22.1, J21.2, J22.2, L2.2, U2.4 (FB)
unnamed: C31.1, J40.2, J42.2, R4.1, U3.1 (VIN)
unnamed: C32.1, J31.2, J32.2, L3.2, U3.4 (FB)
unnamed: D1.1 (K), L1.1, U1.2 (OUT)
unnamed: D2.1 (K), L2.1, U2.2 (OUT)
unnamed: D3.1 (K), L3.1, U3.2 (OUT)
unnamed: D4.2 (A), R4.2
unnamed: F41.1, F42.2, J42.1
unnamed: F41.2, J43.2, J44.2
unnamed: R11.1, R12.2
unnamed: R11.2, U1.4 (FB)

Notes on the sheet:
5V logique
5V puissance
12V puissance
BAT
arret urgence NC
puissance moteurs
Hack feedback 5.74 KOhms

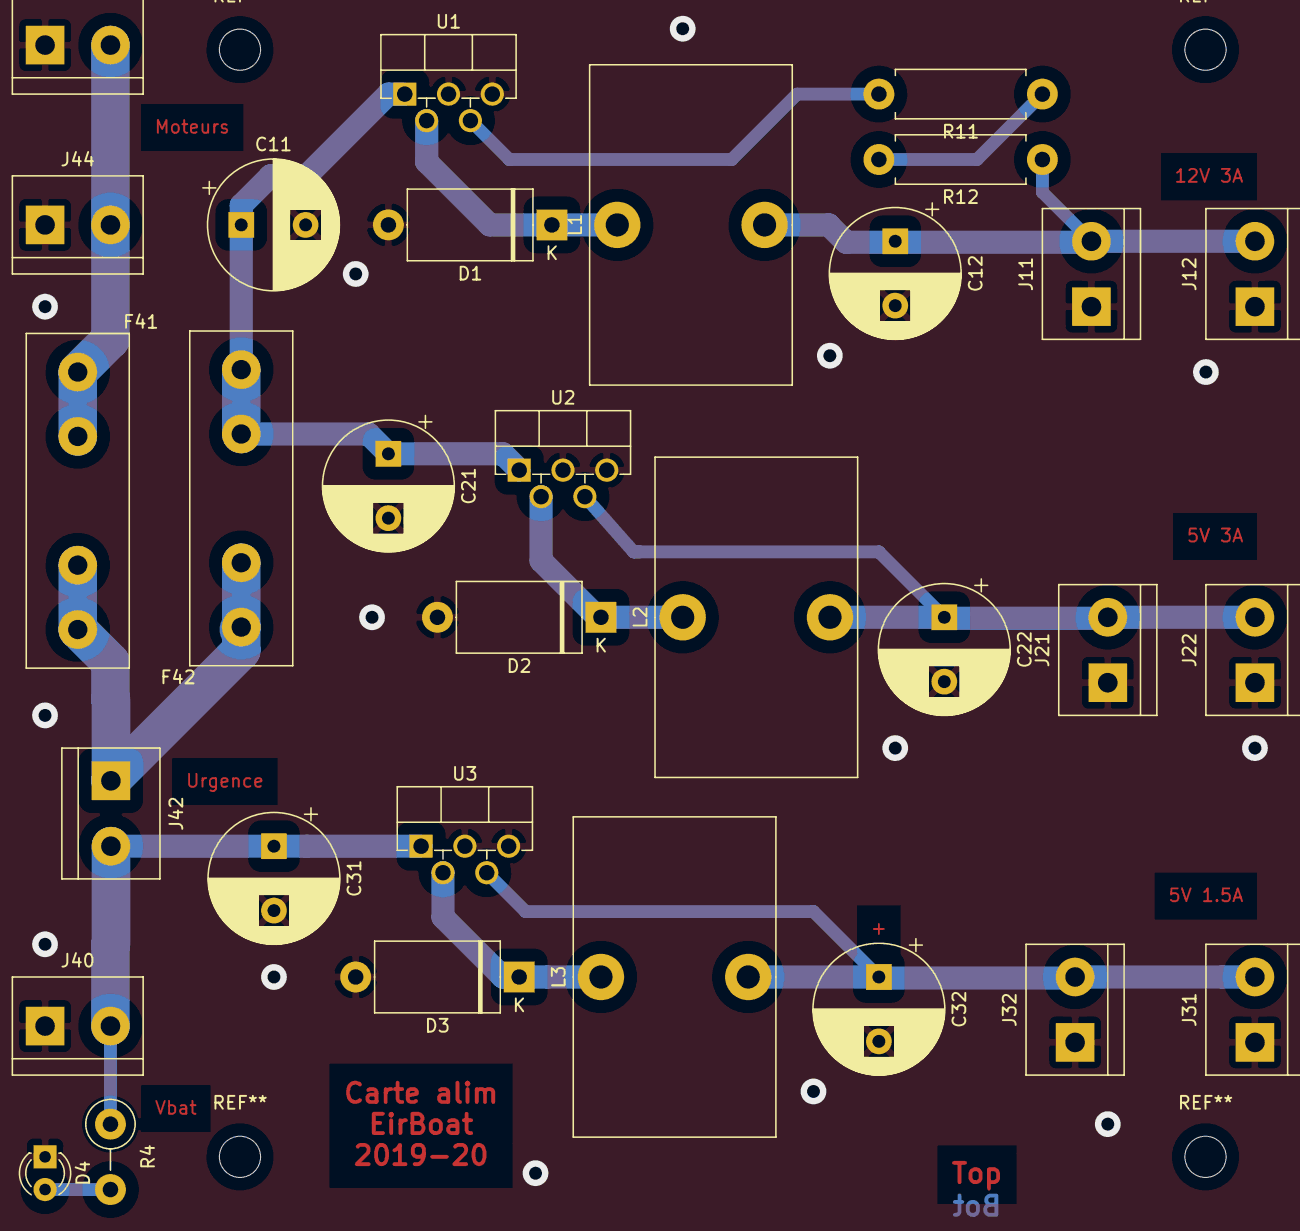
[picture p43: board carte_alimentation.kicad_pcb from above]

Board: 2 copper layers, 31 parts (0 on the bottom side), 14 nets.

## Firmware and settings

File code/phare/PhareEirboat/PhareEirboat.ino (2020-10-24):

#include <ServoTimer2.h>
#include <VirtualWire.h>

ServoTimer2 ServoBas1;
ServoTimer2 ServoBas2;
ServoTimer2 ServoCentre;
ServoTimer2 ServoHaut;

//Cablage
#define SERVOPinBas1 9
#define SERVOPinBas2 8
#define SERVOPinCentre 7
#define SERVOPinHaut 6
#define POTAR 5
#define MOTEUR 5

//Seuils pour les valeurs limites du potar et des servos
#define SEUIL_POTAR_BAS 150
#define SEUIL_POTAR_HAUT 500

#define SEUIL_HAUT_BAS1 30
#define SEUIL_BAS_BAS1 200
#define SEUIL_INTER_BAS1 (SEUIL_HAUT_BAS1 + SEUIL_BAS_BAS1)/2 - 30

#define SEUIL_HAUT_BAS2 152
#define SEUIL_BAS_BAS2 0

#define SEUIL_HAUT_CENTRE 50  //delta = -62
#define SEUIL_BAS_CENTRE 110
#define SEUIL_INTER_CENTRE 180

#define SEUIL_HAUT_HAUT 100  //delta = +96
#define SEUIL_BAS_HAUT 10
#define SEUIL_INTER_HAUT 140

//Etats du bras
#define BAS 0
#define HAUT 1

bool etat = BAS;   //Memoire de l'etat du bras
const char msg[8] = "31415926";   //Message envoyé par le phare pour confirmer l'ascention

int vitesse = 10; //en millisecondes

void setup() {
  ServoBas1.attach(SERVOPinBas1);
  ServoBas2.attach(SERVOPinBas2);
  ServoCentre.attach(SERVOPinCentre);
  ServoHaut.attach(SERVOPinHaut);

  ServoBas1.writeServo(SEUIL_BAS_BAS1);
  ServoBas2.writeServo(SEUIL_BAS_BAS2);
  ServoCentre.writeServo(SEUIL_BAS_CENTRE);
  ServoHaut.writeServo(SEUIL_BAS_HAUT);
  
  pinMode(MOTEUR, OUTPUT);
  digitalWrite(MOTEUR, LOW);

  vw_setup(2000);
  
  delay(1000);
}

void loop() {
  int val = analogRead(POTAR);
  if( val < SEUIL_POTAR_BAS || val > SEUIL_POTAR_HAUT) {
    if(elevation()){
      RF_OK();
    }
  }
  else {
    descente();
  }
}

bool elevation() { 
  if(!etat){
    int j;
    for(j = SEUIL_BAS_BAS1; j >= SEUIL_INTER_BAS1; j--){
      ServoBas1.writeServo(j);
      delay(vitesse);
    }
    delay(1000);
    for(int i = SEUIL_BAS_HAUT; i <= SEUIL_INTER_HAUT; i++) {
      ServoHaut.writeServo(i);
      ServoCentre.writeServo(map(i, SEUIL_BAS_HAUT, SEUIL_INTER_HAUT, SEUIL_BAS_CENTRE, SEUIL_INTER_CENTRE));
      delay(vitesse);
    }
    delay(1000);
    for(j = SEUIL_INTER_BAS1; j >= SEUIL_HAUT_BAS1; j--){
      ServoBas1.writeServo(j);
      if(j - SEUIL_HAUT_BAS1 < (SEUIL_INTER_CENTRE - SEUIL_HAUT_CENTRE)/2) {
        ServoCentre.writeServo(map(j, SEUIL_HAUT_BAS1+(SEUIL_INTER_CENTRE - SEUIL_HAUT_CENTRE)/2, SEUIL_HAUT_BAS1, SEUIL_INTER_CENTRE, SEUIL_HAUT_CENTRE));
        ServoHaut.writeServo(map(j, SEUIL_HAUT_BAS1+(SEUIL_INTER_CENTRE - SEUIL_HAUT_CENTRE)/2, SEUIL_HAUT_BAS1, SEUIL_INTER_HAUT, SEUIL_HAUT_HAUT));
      }
      delay(vitesse);
    }

    delay(1500);
    digitalWrite(MOTEUR, HIGH);
    etat = HAUT;
    
  }
  
  return etat;
}

void descente() {
  int servoBas1 = SEUIL_HAUT_BAS1;
  int servoBas2 = SEUIL_HAUT_BAS2;
  int servoCentre = SEUIL_HAUT_CENTRE;
  int servoHaut = SEUIL_HAUT_HAUT;

  digitalWrite(MOTEUR, LOW);
  
  while(etat){
    ServoBas1.writeServo(servoBas1++);
    //ServoBas2.write(servoBas2--);        //Non utilisé
    if (servoHaut != SEUIL_BAS_HAUT && servoBas1 > 60) {
      ServoHaut.writeServo(servoHaut--);
    }
    if (servoCentre != SEUIL_BAS_CENTRE ){
      ServoCentre.writeServo(servoCentre++);
    }
    
    if(servoBas1 == SEUIL_BAS_BAS1) {
      etat = BAS;
    }
    
    delay(vitesse);
  }
}

void RF_OK(){
  vw_send(msg, 8);
  vw_wait_tx();
  delay(5000);
}

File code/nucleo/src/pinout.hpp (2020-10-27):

#ifndef __PINOUT_H_
#define __PINOUT_H_


// moteur gauche
#define break_G_PIN D5
#define PWM_G_PIN D6
#define dir_G_PIN D7

// moteur droit
#define break_D_PIN PE_8
#define PWM_D_PIN D3
#define dir_D_PIN D4

// bluetooth serie
#define TX_BLUE_PIN PB_10
#define RX_BLUE_PIN PB_11

//GP2 avant
#define GP2_A1_PIN PF_4
#define GP2_A2_PIN PC_2
#define GP2_A3_PIN PB_1

//GP2 arriere
#define GP2_R1_PIN PF_9
#define GP2_R2_PIN PF_7
#define GP2_R3_PIN PF_8

//servo gauche PWM
#define BRAS_G_PIN PB_11

//servo droit PWM
#define BRAS_D_PIN PA_0

//pavillon
#define PAVILLON_PIN PC_6


//contacteurs
// #define CTC_1_PIN PC_8
// #define CTC_2_PIN PC_6
#define CTC_3_PIN PG_0
#define CTC_4_PIN PE_0

// BONUS
#define bonus_1_PIN PD_7
#define bonus_2_PIN PD_6
#define bonus_3_PIN PD_5
#define bonus_4_PIN PD_4
#define bonus_5_PIN PD_3



#endif // __PINOUT_H_

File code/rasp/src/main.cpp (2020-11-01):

#include "main.hpp"
#include <sys/time.h>
#include <signal.h>
#include <stdio.h>
#include <string.h>

using namespace std;
using namespace std::chrono;

class Navigation;
class GP2;
class Robot Robot;
bool debug=false;
vector<Node> debugPath(2);
int total_optimized;
int unoptimized;
int total_deplacement;
int success_deplacement;
int success_reach;
int total_reach;
int timeout;
int robot_adv;
int timeout_after_timeout;
string side = "blue";
bool in_port=false;
int pc=0;
std::chrono::steady_clock::time_point BeginMeasurement;

//Définition des points d'interets
struct Node Phare_blue={20,20,0,0,0,0,0};
struct Node Phare_yellow={20,180,0,0,0,0,0};
struct Node Phare_blue_waypoint={50,45,0,0,0,0,0};
struct Node Phare_yellow_waypoint={50,155,0,0,0,0,0};
struct Node Manche_1_blue={23,(180),0,0,0,0,0};
struct Node Manche_2_blue={63,(180),0,0,0,0,0};
struct Node Manche_1_yellow={23,(20),0,0,0,0,0};
struct Node Manche_2_yellow={63,(20),0,0,0,0,0};

struct Node Port={20,(80),0,0,0,0,0};
struct Node Port_N={20,50,0,0,0,0,0};
struct Node Port_S={20,150,0,0,0,0,0};

// Parse opt
void parse_opts(int argc, char *argv[], int *pc, string *side){
  // Default values
  *pc = 0;
  int opt;
  while ((opt = getopt(argc, argv, "p:")) != -1) {
    switch (opt) {
      case 'p':
        *pc = atoi(optarg);
        break;
    }
  }
}

//Initialisation
void setup()
{
  LowLevel LowLevel;
  //Information sur le côté de la table
  printf("Je récupère l'information du côté de la table............ \n");
  side=Robot.calibration();
  if (side=="blue") {
    printf("\033[34mJe suis du côté bleu !\033[0m \n");
    go_to({.x=16,.y=80});
  }
  else if(side=="yellow"){
    printf("\033[33mJe suis du côté jaune !\033[0m \n");
    go_to({.x=16,.y=120});
  }
  printf("Je commence la calibration des GP2........................\n");
  Robot.detection('a', '0');

  printf("Je vérifie que mes bras fonctionnent......................\n");
  Robot.actionneur(0, 1);
  Robot.actionneur(0, 0);
  Robot.actionneur(1, 1);
  Robot.actionneur(1, 0);

  printf("J'initialise l'afficheur de score ........................\n");
  Robot.setup_score();
  Robot.set_score(0);
  if (side=="blue") {
    go_to({.x=20,.y=80});
  }
  else if(side == "yellow"){
    go_to({.x=20,.y=120});
  }
  int i=0;
  while (i<=10) {
    if(Robot.depart()==true){
      i++;
    }
    printf("Je suis pret en attente du départ ! \r");
  }
  BeginMeasurement=steady_clock::now();
}

void port_now_blue (std::chrono::steady_clock::time_point BeginMeasurement)
{
  Robot.detection('a', '0');
  while ((steady_clock::now()-BeginMeasurement)<milliseconds{95000}) {

  }
  auto delai = steady_clock::now() - BeginMeasurement;
  std::cout << "Temps total d'execution " << duration_cast<milliseconds>(delai).count() << " ms" << '\n';
  Robot.pavillon(1);
  Robot.add_score(10);
  if(in_port==false){
  if (Robot.communication_boussole()==0) {
    go_to({.x=20,.y=50});
    Robot.add_score(10);
    }
    else if(Robot.communication_boussole()==1){
      go_to({.x=20,.y=150});
      Robot.add_score(10);
    }
  }
    while (1) {

    }
}

void port_now_yellow (std::chrono::steady_clock::time_point BeginMeasurement)
{
  Robot.detection('a', '0');
  while ((steady_clock::now()-BeginMeasurement)<milliseconds{95000}) {

  }
  auto delai = steady_clock::now() - BeginMeasurement;
  std::cout << "Temps total d'execution " << duration_cast<milliseconds>(delai).count() << " ms" << '\n';
  Robot.pavillon(1);
  Robot.add_score(10);
  if(in_port==false){
  if (Robot.communication_boussole()==0) {
    go_to({.x=20,.y=150});
    Robot.add_score(10);
  }
    else if(Robot.communication_boussole()==1){
      go_to({.x=20,.y=50});
      Robot.add_score(10);
    }
  }
    while (1) {

    }
}


//Boucle de jeu
void loop_blue(std::chrono::steady_clock::time_point BeginMeasurement)
{
  int temps=0;
  Robot.detection('a','0');
  printf("\033[33mJe pars du PORT et je vais au WAYPOINT \033[0m \n");
  go_to({.x=50,.y=45});
  printf("\033[33mJe pars du WAYPOINT et je vais au PHARE \033[0m \n");
  go_to({.x=20,.y=20});
  Robot.actionneur(1,1);
  go_to({.x=37,.y=22});
  Robot.actionneur(1, 0);
  // if (Robot.communication_phare()==false) {
  //   go_to({.x=37,.y=22});
  //   Robot.actionneur(0, 1);
  //   go_to({.x=20,.y=22});
  //   Robot.actionneur(0,0);
  // }
  if (Robot.communication_phare()==true) {
    Robot.add_score(15);
  }
  else {
    Robot.add_score(5);
  }

  //Module Manche à air
  printf("\033[33mJe pars de PHARE et je vais à MANCHE_1 \033[0m \n");
  Robot.detection('a', '1');
  if (steady_clock::now() - BeginMeasurement > milliseconds{85000}) {
    port_now_blue(BeginMeasurement);
  }
  go_to({.x=70,.y=110 });
  Robot.detection('a', '0');
  Robot.actionneur(0, 1);
  go_to({.x=57,.y=182});
  if (steady_clock::now() - BeginMeasurement > milliseconds{85000}) {
    port_now_blue(BeginMeasurement);
  }
  Robot.rotation(180);
  Robot.actionneur(0,0);
  Robot.add_score(5);//10
  while (steady_clock::now() - BeginMeasurement < milliseconds{30000}) {
    printf("J'attend la calibration de boussole \r");
  }
  printf("\033[33mJe récupère l'information de la boussole \033[0m \n");
  int boussole=Robot.communication_boussole();
  printf("\033[33mJe pars du MANCHE_2 et je vais au PORT %d \033[0m \n",boussole);
  if (boussole==true) {
    go_to({.x=20,.y=50});
    Robot.add_score(10);
  }
  else if(boussole==false){
    go_to({.x=20,.y=150});
    Robot.add_score(10);
  }
  in_port=true;
  auto delai = steady_clock::now() - BeginMeasurement;
  std::cout << "Temps total d'execution " << duration_cast<milliseconds>(delai).count() << " ms" << '\n';
  while (steady_clock::now()-BeginMeasurement < milliseconds{85000}) {

  }
  port_now_blue(BeginMeasurement);
}
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

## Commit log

2020-01-16 Création de la fonction summarize
2020-01-16 Ajout des constantes de debug
2020-01-16 Ajour des constantes de debug
2020-01-16 Création de summarize
2020-01-19 ajout des tests protocoles dans le makefile, probleme de reference à régler
2020-01-19 Début de complétion de la phase d'initialisation
2020-01-19 Numérotation de l'éco cup du port nord et du port sud
2020-01-19 Modification de la ddernière étape, ajout de l'idée de port Nord et Sud
2020-01-19 On règle les bétise de Ptit Lu
2020-01-19 Ajout fonction angle et supression de backword et forward
2020-01-19 Ajout de la fonctionne de détection (attente de mise en place de test)
2020-01-19 Décision de n'avoir que 3 GP2 actifs, la nucléo gère quel coté est actif et la rasp gère l'activation général des GP2
2020-01-19 Mise à jour main pour être en accord avec les différents avancement
2020-01-19 Création des fonctions de requete
2020-01-19 Création des fonctions de requetes
2020-01-19 Mise à jour mineur des tests
2020-01-21 Modification des fonctions d'affichages (pour que ça soit toujours plus beau)
2020-01-21 Modification du type de retour de call_back, renvoie l'état de la requette (0 = ok , 1 = timeout , 2 = detection) Ajout de la fonction call_back pour calculer ça de manière propre
2020-01-21 Modification de Navigate_to_asserv, quand on reconstruit la fonction on verifie le back, création de back_effect pour avoir un comportement adapté
2020-01-21 Modification des test, ajout d'une detection forcée en 38 58
2020-01-22 Changement des fonctions de retour sur l'asservissement
2020-01-25 les bons fichiers c'est mieux
2020-01-29 ajout des dernières commandes des deux côtés
2020-01-29 Ajout de la fonction stun qui permet de se débloquer d'une situation totalement fermée
2020-01-30 changement fonctions publiques protocole
    les get retournent un code d'etat, les valeurs sont retournées via des
    pointeurs en parametre
    ajout commentaire pour les fonctions publiques
2020-01-30 mise en place timeout sur les return
2020-02-01 creation de la classe protocole
    classe protocole fonctionnelle, s'inspirer du main.cpp pour l'utilisation
2020-02-01 changment main nucleo, corrections cote rasp
    [main.cpp]
2020-02-01 Début des tests avec protocole de com
2020-02-01 Compilation de protocole
2020-02-03 Avancée des test
2020-02-03 nettoyage printf
2020-02-07 Modification mineurs (changement de compilateur)
2020-02-07 Test avec obstacles et la nucléo
2020-02-07 Rajout de protocole dans la détection
2020-02-08 Début des codes sur la nucléo
2020-02-16 modif makefile cross compilation
    ajouter parametre cross=1 à make pour faire un executable pour la rasp
2020-02-17 Ajout print panic
2020-02-17 Maj rapport de description du robot et ajout de learn Makefile
2020-02-17 Commentaire print
2020-02-17 Modif quelques prototypes
2020-02-20 MAJ dossier de présentation part
2020-03-08 ajout prise en compte des actionneurs
2020-03-10 PRemier pas avec les servo
2020-03-10 Ajout acctionneur dans main.cpp de nucléo
2020-03-12 ajout action servo proto
2020-03-12 Faire mumuse avec les actionneurs
2020-03-22 Supression des *.gcno en make clean
2020-03-22 Supression des fichier objets + création dossier phare
2020-03-24 Ajout 1ère version Code Balise
    Ajout de la 1ère version du code de la balise.
    Code non optimisé pour le moment et ne discrimine pas le tag 17.
    Ne prends pas encore en compte le module sans fil.
2020-03-26 Ajout de la dernière réunion
2020-04-19 Documentation : Ajout de la documentation du dossier rasp/
2020-04-19 Documentation : Ajout de la documentation sur la balise
2020-04-19 Documentation : fin de la documentation
2020-04-20 Test : Création de la structure de test
2020-04-20 Ajout de quelques tests de navigation
2020-04-20 Test : ajout des derniers test sur la navigation
    Coverage actuel 82%
2020-05-26 Mise à jour de choses mineures
2020-08-09 nettoyage erreurs et warnings
    changement des noms de bibliothèque et warning du a l'utilisation de la
    fonction wait au lieu de wait_us
2020-09-14 ajout schema global des connections
2020-09-26 Add files via upload
    Code asserv de position
2020-09-26 penser bete fonction poll
    la fonction poll risque de tout bloquer ouiiii
2020-09-27 ajout test gp2
    lecture tension
2020-09-28 calcul angle du robot avec changement de sens de marche
2020-10-06 vers l'absolu et l'au-dela !
    des coordonnées qui fonctionnent ça serait mieux
2020-10-09 les memes unités c'est mieux
    go_XY ça marche <3 (tests complémentaires)
2020-10-10 goXY approximatif
    on peut envoyer des commandes du protocole
    feedback protocole a faire
2020-10-12 setup cmake crosscompilation
    correction Cmakelists
    creation d'un fichier pour setup la toolchain de cross compilation
2020-10-17 fix updatebuffer
    on arrive a lire les données et timeout correctement
2020-10-18 fix some minors problems
    [main.cpp]
2020-10-22 fix offset pwm quand negatif
2020-10-24 fix led jaune
2020-10-25 init x0 y0
    pour le changement de coté
    maintenant la première commande SPOx,y recue apres un RESET set
    le x0 y0 du robot
2020-10-25 maj meca
    [Assemblage.0003.iam, Assemblage.iam, Assemblage.stl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]
2020-10-25 fix premiere commande SPOx0,y0
    [main.cpp]
2020-10-25 add pin et fonctions pwm bras
2020-10-26 Livraison Final Balise
    Nouvelle (et dernière) version du code balise avec communication vers la nano-arduino qui envoi le signal au robot.
2020-10-27 creation process_GP2
    ignore les obstacles en dehors de la table et du bord de la table
2020-10-29 mode panic asserv
    recule de 3 cm
